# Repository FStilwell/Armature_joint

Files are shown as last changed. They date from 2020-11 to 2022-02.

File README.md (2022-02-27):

# Armature_joint
This repository serves as a location for relevant work regarding the Armature Joint module as my Level 7 Engineering Development Project at WelTec.

## Overview

In-depth details on the project can be found in the "project_report.pdf" file in the "documentation" folder.

### Mechanical Structure

The solidworks 3D files for the joint modules can be found in the "Mechanical_structure" folder. The solidworks files are quite messy with unorganised links in the model. Therefore, I would recommend that the concepts would be used rather than building directly from the solidworks files.

The details behind my thinking with the mechanical structure can be  found in the project report under the "5. Project Design/methodology" section.

### Electronics

All the electronics files and information are found under the "PCB" folder. More in-depth details on the electronics are found in the project report under the "5. Project Design/methodology" section.

#### Rework and test info

A document with the test info for each of the boards is found under the PCB/Board_testing directory. There are a few LEDs that were placed incorrectly and there's a design error with the reset button.

### Software

More details on the software can be found in the project report under the "5. Project Design/methodology" section.

The software that I worked on is found under SDKs/nRF5_SDK_14.2.0_17b948a/examples/my_examples. They are Segger Embedded Studio project files. There are two programs that I think might be useful which are the blinky projects below.

A blink program is found under SDKs/nRF5_SDK_14.2.0_17b948a/examples/my_examples/Armature_joint_blinky_4-working/

A BLE blink program is found under SDKs/nRF5_SDK_14.2.0_17b948a/examples/my_examples/ble_app_blinky-working/

#### Configuring projects to work with the Armature boards

A guide I wrote for configuring the Segger Embedded Studio example projects to work with the armature boards can be found at Documentation/Modifying_SDK_SES_examples_for_Armature.pdf

#### Programming the boards

Using the Segger J-Link Edu Mini and a custom ribbon cable with a 6 pin header, I was programming the boards using the native Segger Embedded Studio toolchain. The header is connected to to the board as shown in the image below.



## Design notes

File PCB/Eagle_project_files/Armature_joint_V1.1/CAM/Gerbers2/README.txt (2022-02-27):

Board Dimensions:
 Approximately 35mm X 35mm circular
 2 Layers
 1.6mm Thickness	
 Silkscreen on top layer only

Gerber Files:

copper_bottom.gbr - Bottom layer

copper_top.gbr - Top layer

Soldermask offset per your process.

Special Instructions:
No added copper around the PCB antenna where ground planes stop

Contact info:

traveler.hauptman@mechadept.com

022 627 1529

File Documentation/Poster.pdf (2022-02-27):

`

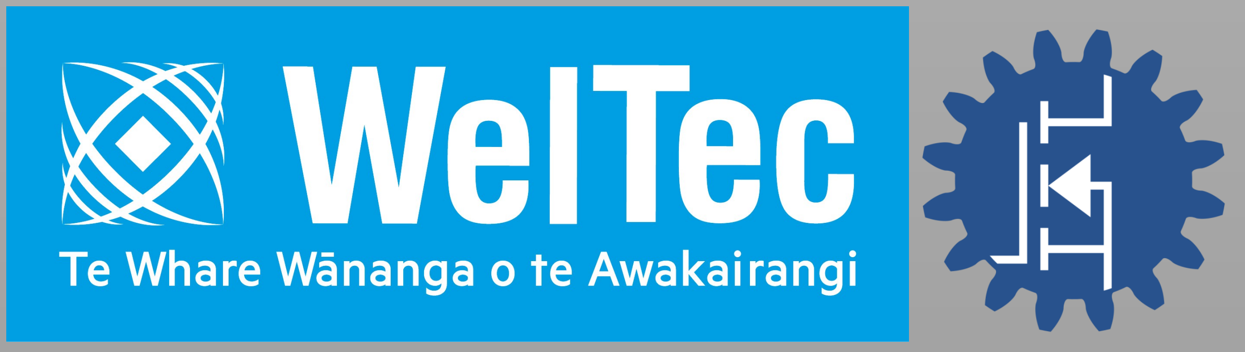
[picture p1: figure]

# Armature Joint Module

Prototyping large robots at a miniature scale is a great way to validate a robot’s design. It allows the engineer to test a robot’s kinematic structure design and its range of motion in the real world, at a low cost. MechAdept employs this method for their high-performance mechatronic systems, but they do not give useful joint position feedback without manual measurement. The aim of this project was to develop a functional prototype of a single joint module to prove the concept of a puppeteering armature which would be manipulated by hand and stream out position information to a user terminal via Bluetooth. This is for MechAdept to prototype robotics and present to clients a virtual puppeteered armature. The design had to be compact, battery powered, modular and simple.

By:
Flynn Stilwell

Supervisor:
Frank Beinersdorf

Client:
MechAdept

This project required the development of systems of three different types; mechanical, electronic, and embedded software.

LinkedIn

### Kinematic Structure

3D printing was used for its fast turnaround time of mechanical prototypes and its availability. 3D printing design considerations were then researched before designing concepts were produced.
The kinematic structure was rapidly prototyped using Solidworks 3D CAD software for the modelling and 3D printing for the manufacturing. Two main concepts were produced and evaluated, and the preferred one was iterated upon to experimentally validate design decisions. The first concept relied on the magnetic pull of a magnet to hold the links together and provide field position to the magnetic sensor, however the prevailing concept was a snap-fit type which relied on a clip-on profile to interface the two links. This offers a rigid connection, a holding torque due to friction in the joint interface and a simple solution.

Link 2: Holds the magnet with a press-fit and the male snap-fit tabs to interface with link 1.

Magnet: Diametrically magnetised for easy interface with the magnetic sensor on the PCB

Link 1: Provides the female slot for the snap-fit connection and an enclosure for the PCB and battery. The slot allows rotation of link 1 and provides friction and hence a holding torque.

Custom PCB: Powered by a Lithium-Polymer battery, the custom PCB features a Bluetooth-capable System on Chip (SoC), PCB trace antenna, 3D hall sensor for field position measurement, battery charging circuitry and a 3.3V voltage regulator.

Link 1 cap: Closes the enclosure and secures the PCB and battery.

# Overview

Prototype 4, disassembled

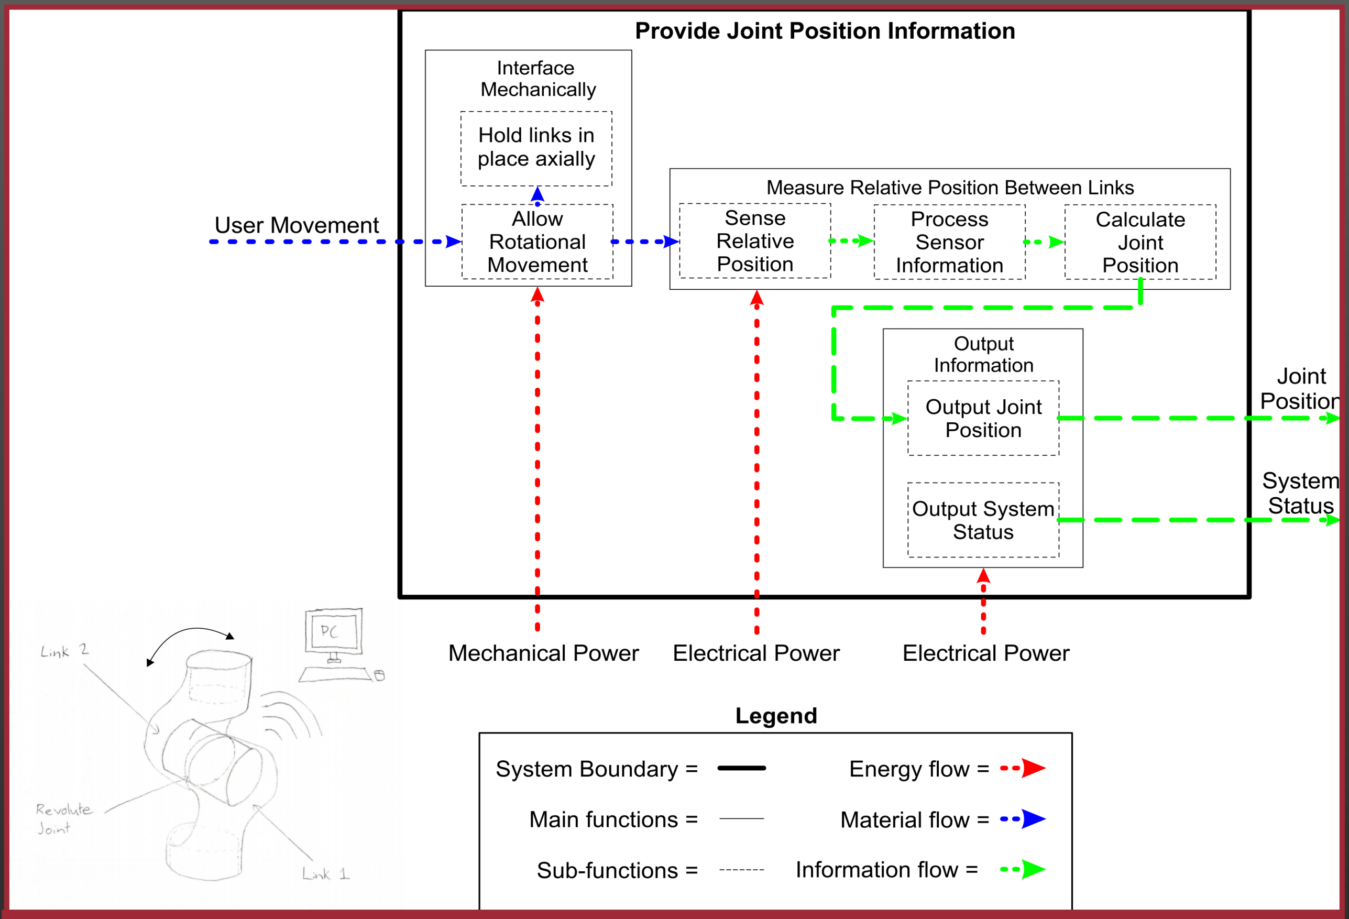
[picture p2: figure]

Function Structure Analysis for Problem identification

### Electronic System

The electronic system elements were prototyped on a breadboard to validate the magnetic position measurement system. High speed signal Printed Circuit Board (PCB) design considerations and electronic components were researched for implementing the design on a PCB. This was designed electronically using Autodesk Eagle, manufactured by PCBZone in NZ, and assembled with the help of MechAdept.
Reference circuitry from Nordic Semiconductor was used for the Bluetooth-capable System on Chip (SoC) section of the PCB to help ensure its sufficient Radio Frequency (RF) performance.

### Embedded Software

The Segger Embedded Studio Integrated Development Environment (IDE) was used to write software and program the custom board and nRF52 development dongle. Segger’s J-Link debugging probe was used with the IDE for code debugging. Nordic Semiconductor’s Software Development Kit (SDK) was used to learn the microcontroller platform and provide a base for the embedded software using the method of studying and modifying example code.

# Development

Assembly Process

Solder paste applied | Components Placed

Reflow soldering process

`

# Latest Prototype

Concept 1—magnetic
interface

Concept 2—Snap-fit interface

### Conclusion

Multiple mechanical test iterations have been produced and the best mechanical interface was found to be a snap-fit design with a balance of actuation friction, simplicity, and ease of assembly/disassembly.
Six of the PCB’s have been produced, all of which have passed power cycle tests, and one has been programmed with a basic Bluetooth application which verified the operation of the electronic system. The connection was maintained over a distance of >10m. The functionality of the joint remains unproven due to the complexity of the embedded software. The level of knowledge required was beyond the scope of this programme, but this project has presented the motivation for future learning.
This project involved the development of a single joint module. It provided the hardware platform to build upon. However, the vision is to have multiple of these connected to interchangeable links to provide a hand manipulated virtual model and miniature robot prototyping platform.

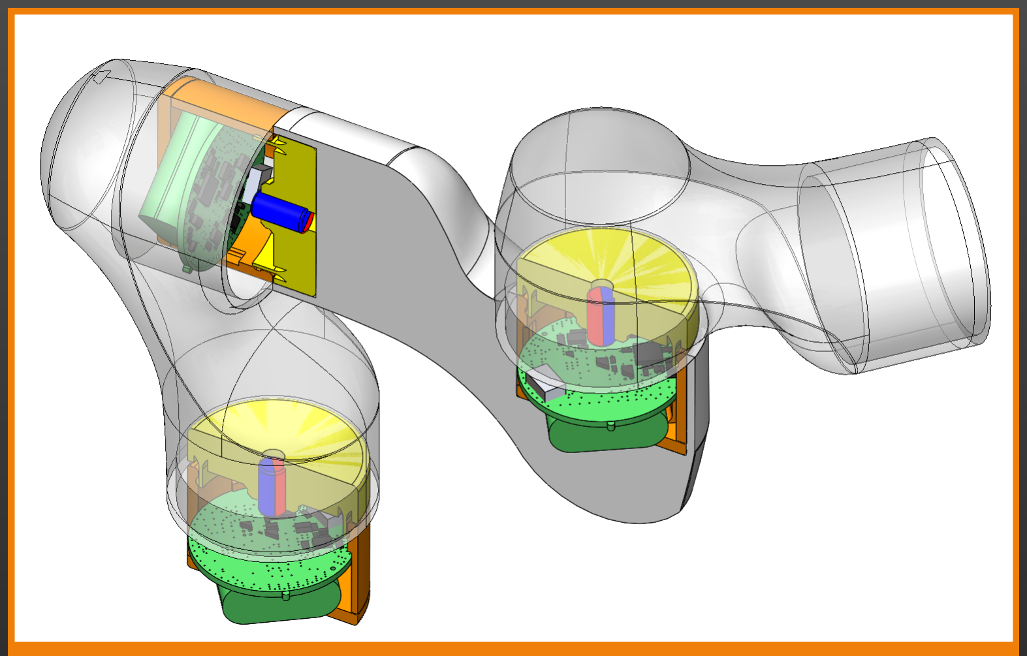
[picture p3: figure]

Envisioned armature implementation by Frank

Latest prototype
assembled,
indicating BLE
advertisement
with green LED

nRF42810 SoC

RGB indicator
LED

3.3V Voltage
Regulator

Lithium Polymer/
Ion battery charger

3D Hall Sensor

PCB trace antenna

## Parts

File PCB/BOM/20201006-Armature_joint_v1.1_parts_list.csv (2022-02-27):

Index | Quantity | Part Number | Manufacturer Part Number | Description | Customer Reference | Available | Backorder | Unit Price | Extended Price NZD
1 | 5 | 1490-1062-ND | NRF52810-QCAA-T | IC RF TXRX+MCU BLUETOOTH 32WFQFN |  | 5 | 0 | 5.30000 | 26.50
2 | 35 | 490-7998-1-ND | GCM155R71C104KA55J | CAP CER 0.1UF 16V X7R 0402 |  | 35 | 0 | 0.08900 | 3.12
3 | 10 | 311-1024-1-ND | CC0402JRNPO9BN101 | CAP CER 100PF 50V C0G/NPO 0402 |  | 10 | 0 | 0.03200 | 0.32
4 | 20 | 311-1446-1-ND | CC0603KRX7R7BB105 | CAP CER 1UF 16V X7R 0603 |  | 20 | 0 | 0.14000 | 2.80
5 | 25 | 311-3609-1-ND | CC0402GRNPO9BN120 | CAP CER 12PF 50V NPO 0402 |  | 25 | 0 | 0.08100 | 2.03
6 | 5 | 490-XRCGB32M000FXH2CR0CT-ND | XRCGB32M000FXH2CR0 | CRYSTAL 32.0000MHZ 8PF SMD |  | 5 | 0 | 0.74000 | 3.70
7 | 5 | CKN10503CT-ND | PTS810 SJK 250 SMTR LFS | SWITCH TACTILE SPST-NO 0.05A 16V |  | 5 | 0 | 0.54000 | 2.70
8 | 5 | 754-2143-1-ND | APHF1608LSEEQBDZGKC | LED RGB CLEAR 4SMD |  | 5 | 0 | 1.28000 | 6.40
9 | 20 | 311-330LRCT-ND | RC0402FR-07330RL | RES SMD 330 OHM 1% 1/16W 0402 |  | 20 | 0 | 0.02400 | 0.48
10 | 20 | 311-820LRCT-ND | RC0402FR-07820RL | RES SMD 820 OHM 1% 1/16W 0402 |  | 20 | 0 | 0.02400 | 0.48
11 | 6 | TC1015-3.3VCT713CT-ND | TC1015-3.3VCT713 | IC REG LINEAR 3.3V 100MA SOT23-5 |  | 6 | 0 | 0.61000 | 3.66
12 | 10 | 732-7499-1-ND | 885012205004 | CAP CER 470PF 10V X7R 0402 |  | 10 | 0 | 0.02400 | 0.24
13 | 5 | 609-5379-1-ND | 10118192-0002LF | CONN RCPT USB2.0 MICRO B SMD R/A |  | 5 | 0 | 0.71000 | 3.55
14 | 20 | 490-10884-1-ND | GRJ188C70J475KE11D | CAP CER 4.7UF 6.3V X7S 0603 |  | 20 | 0 | 0.35900 | 7.18
15 | 6 | MCP73831T-2ACI/OTCT-ND | MCP73831T-2ACI/OT | IC CONTROLLR LI-ION 4.2V SOT23-5 |  | 6 | 0 | 0.94000 | 5.64
16 | 6 | 475-3112-1-ND | LB QH9G-N1OO-35-1 | LED BLUE DIFFUSED 0402 SMD |  | 6 | 0 | 0.71000 | 4.26
17 | 20 | 311-10.0KLRCT-ND | RC0402FR-0710KL | RES SMD 10K OHM 1% 1/16W 0402 |  | 20 | 0 | 0.02400 | 0.48
18 | 20 | 311-1.20KLRCT-ND | RC0402FR-071K2L | RES SMD 1.2K OHM 1% 1/16W 0402 |  | 20 | 0 | 0.02400 | 0.48
19 | 10 | 490-11253-1-ND | GJM1555C1HR80WB01D | CAP CER 0.8PF 50V C0G/NP0 0402 |  | 10 | 0 | 0.27300 | 2.73
20 | 10 | 1276-1045-1-ND | CL10A475KQ8NNNC | CAP CER 4.7UF 6.3V X5R 0603 |  | 10 | 0 | 0.06900 | 0.69
21 | 5 | CW100505-3N9JCT-ND | CW100505-3N9J | FIXED IND 3.9NH 840MA 66MOHM SMD |  | 5 | 0 | 0.52000 | 2.60
22 | 5 | 644-1155-1-ND | NX3215SA-32.768K-STD-MUA-9 | CRYSTAL 32.7680KHZ 9PF SMD |  | 5 | 0 | 1.20000 | 6.00
23 | 10 | 587-3292-1-ND | BKP1005EM331-T | FERRITE BEAD 330 OHM 0402 1LN |  | 10 | 0 | 0.09300 | 0.93

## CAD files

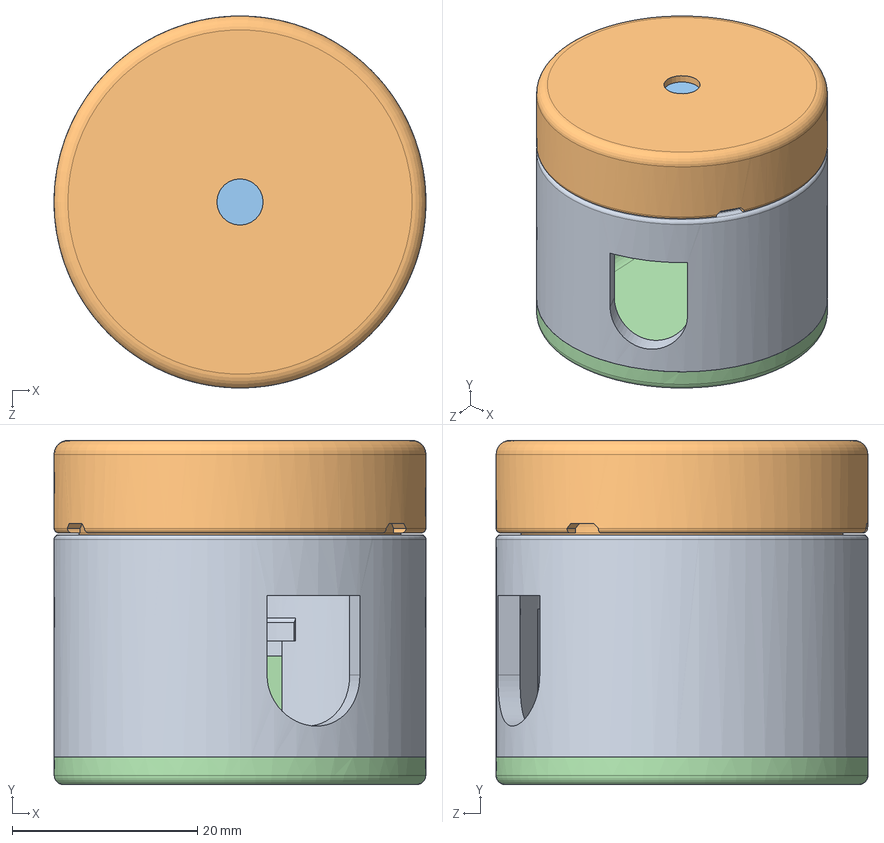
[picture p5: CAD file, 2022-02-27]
Mechanical_structure/Structure_v1.3.SLDASM
40.2 x 37.2 x 40.2 mm
Link1_v1.2
Link2_v1.3
Magnet_model
Link1_cap

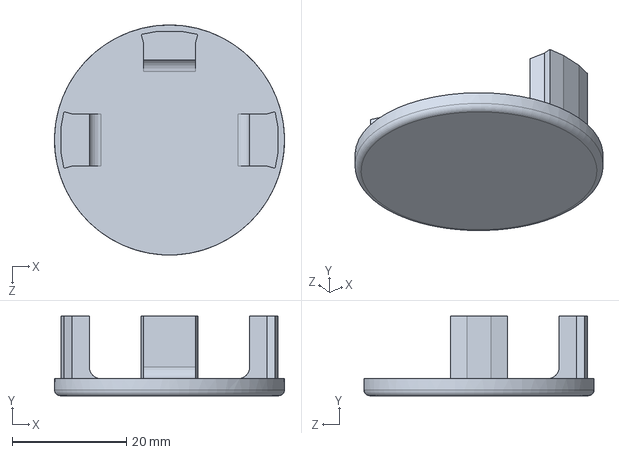
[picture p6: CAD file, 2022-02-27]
Mechanical_structure/Link1_cap.SLDPRT
40.2 x 13.9 x 40.2 mm

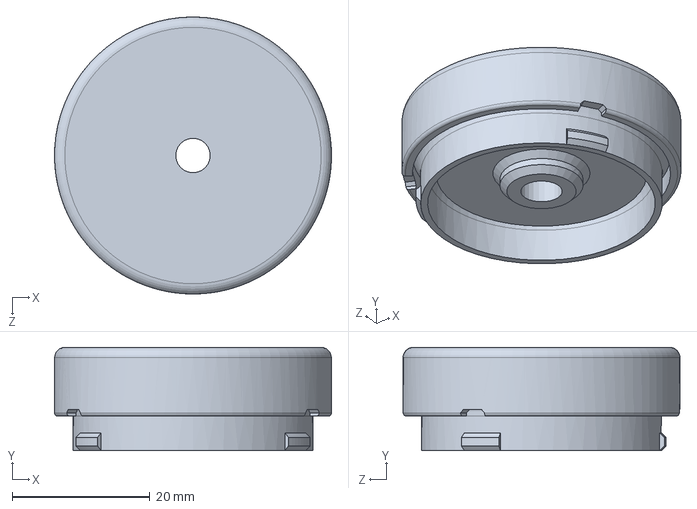
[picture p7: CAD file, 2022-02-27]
Mechanical_structure/Link2_v1.3.sldprt
40.2 x 15.0 x 40.2 mm

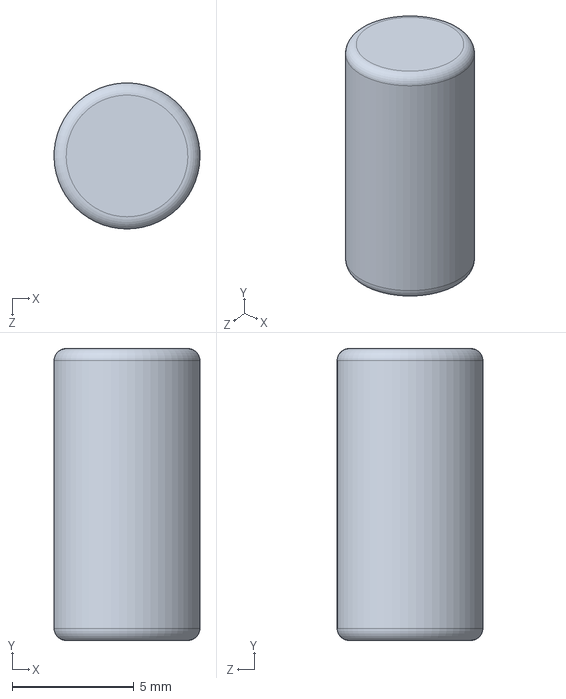
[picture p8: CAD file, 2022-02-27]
Mechanical_structure/Magnet_model.SLDPRT
6.00 x 12.0 x 6.00 mm

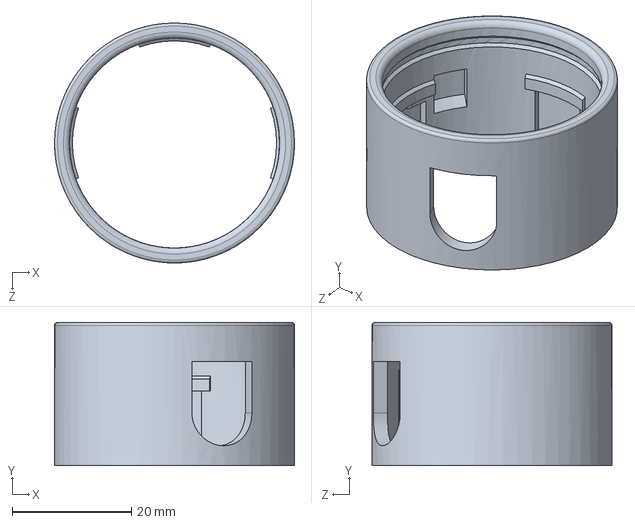
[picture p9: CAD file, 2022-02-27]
Mechanical_structure/Link1_v1.2.SLDPRT
40.2 x 24.0 x 40.2 mm

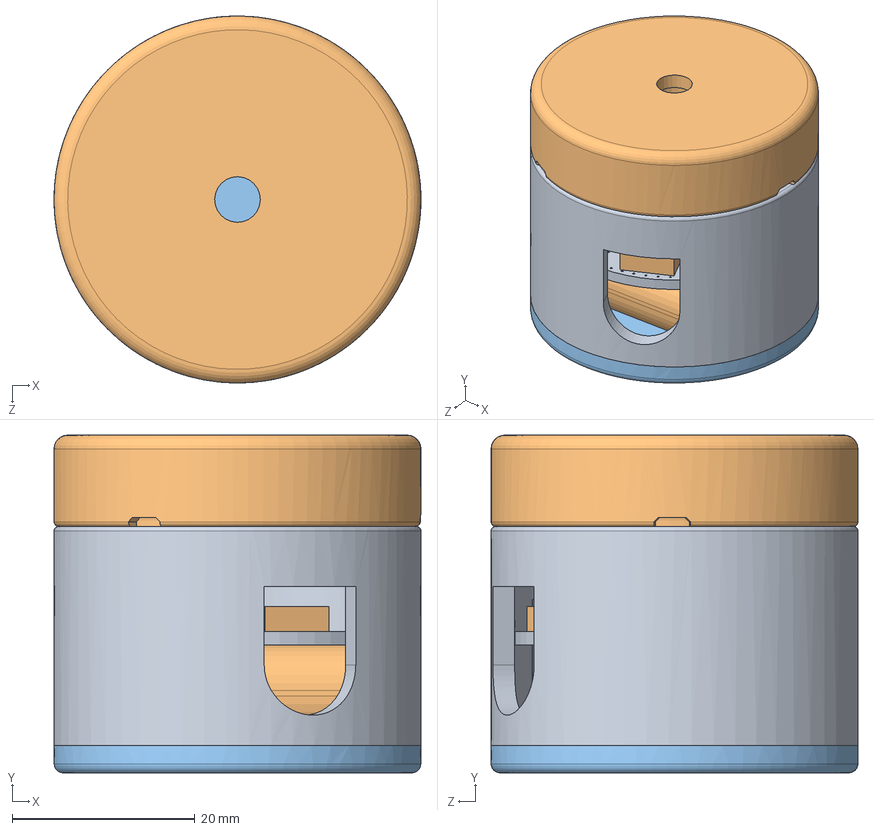
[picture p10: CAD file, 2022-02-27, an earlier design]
Mechanical_structure/Structure_v1.1.SLDASM
40.2 x 37.0 x 40.2 mm
Link1_v1.1
Link2_v1.3
Magnet_model
APHF1608SEEQBDZGKC_KNB-L.step
BT-XTAL_2016_N.step
LED_SML-LX0402SYC-TR_LUM-M.step
PG-TSOP6-6-5_INF.step
PTS810.step
QFN50P500X500X90-32_N.step
RESC0402_M.step x 4
RESC0402_N.step x 20
RESC0603_N.step x 8
SOT-23-5_MC_MCH.step
SOT23-5.step
SWD_6P.step
XTAL_3215_N.step
Board.step
Part1^Armature_Joint_PCB_V1.1
Link1_cap

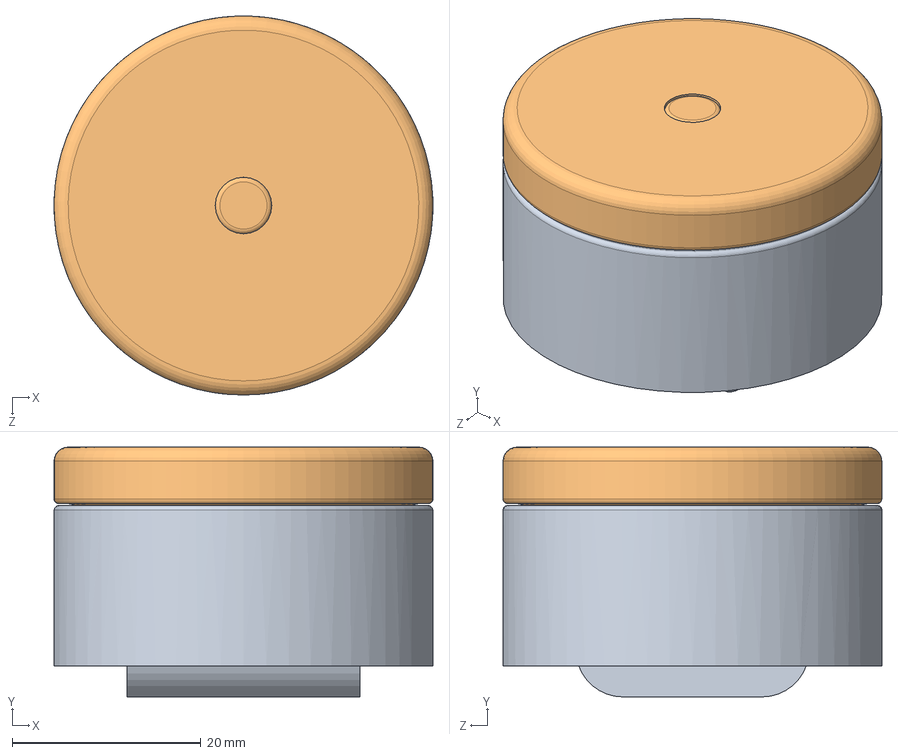
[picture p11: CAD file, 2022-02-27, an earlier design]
Mechanical_structure/Structure_v1.0.SLDASM
40.2 x 26.5 x 40.2 mm
Link1_v1
Link2_v1
APHF1608SEEQBDZGKC_KNB-L.step
BT-XTAL_2016_N.step
LED_SML-LX0402SYC-TR_LUM-M.step
PG-TSOP6-6-5_INF.step
PTS810.step
QFN50P500X500X90-32_N.step
RESC0402_M.step x 4
RESC0402_N.step x 20
RESC0603_N.step x 8
SOT-23-5_MC_MCH.step
SOT23-5.step
SWD_6P.step
XTAL_3215_N.step
Board.step
Part1^Armature_Joint_PCB_V1.1
Magnet_model

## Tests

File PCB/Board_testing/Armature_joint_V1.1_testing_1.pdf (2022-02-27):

PCB Name | Armature Joint V1.1
Serial Number | 3
Tester | Flynn Stilwell
Test Point Diagram

Top View
Test Points | Test Parameters / Conditions | Criterion, Units | Value | Comments
Multimeter Probes | No power connected | Resistance, Ω | 0.1
1-2 | | | OL
1-3 | | | 9.78k
1-4 | | | OL
1-10 | | | 0.0
1-6 | | | 0.0 | Check button, all pins connected to GND. Button pin 4 connected to GND
1-7 | | | 6.12M
1-8 | | | OL
1-9 | | | 6.15M
1-2
1-3 | USB Power Only | Voltage, V
1-4
1-2
1-3 | Battery Power Only | Voltage, V
1-4

Notes:

11.11.20
- RGB LED orientation is wrong
- Button is not functioning due to schematic error, should be removed

PCB Name | Armature Joint V1.1
Serial Number | 4
Tester | Flynn Stilwell
Test Point Diagram

Top View
Test Points | Test Parameters / Conditions | Criterion, Units | Value | Comments
Multimeter Probes | No power connected | Resistance, Ω | 0.3
1-2 | | | OL
1-3 | | | 9.82k | Value from pullup resistor R8, related to GND’d switch
1-4 | | | OL
1-10 | | | 0.1
1-6 | | | 0.1 | Check button, all pins connected to GND. Button pin 4 connected to GND
1-7 | | | 47.2k
1-8 | | | OL
1-9 | | | 6.52M
1-2 | USB Power Only | Voltage, V | 3.987
1-3 | | | 3.343
1-4 | | | 5.074
USB Tester | | Current, A
1-2 | Battery Power Only | Voltage, V 1-3
USB Tester | Power, W

Battery + USB, Charging battery | Current, A
| Voltage, V

Notes:
11.11.20
- RGB LED orientation is wrong
- Button is not functioning due to schematic error, should be removed

PCB Name | Armature Joint V1.1
Serial Number | 5
Tester | Flynn Stilwell
Test Point Diagram

Top View
Test Points | Test Parameters / Conditions | Criterion, Units | Value | Comments
Multimeter Probes | No power connected | Resistance, Ω
1-2 | | | OL
1-3 | | | 9.84k | Value from pullup resistor R8, related to GND’d switch
1-4 | | | OL
1-10 | | | 0.2
1-6 | | | 0.2 | Check button, all pins connected to GND. Button pin 4 connected to GND
1-7 | | | 47.48k
1-8 | | | 9.84k
1-9 | | | 152.0k
1-2
1-3 | USB Power Only | Voltage, V
1-4
1-2
1-3 | Battery Power Only | Voltage, V
1-4

Notes:
11.11.20
- LD2, charger indicator orientation is wrong
- BLE Blinky program upload: Indicates advertisement but cannot be found with nRF Connect Android
- C1 possibly disconnected
- Button is not functioning due to schematic error, should be removed

PCB Name | Armature Joint V1.1
Serial Number | 6
Tester | Flynn Stilwell
Test Point Diagram

Top View
Test Points | Test Parameters / Conditions | Criterion, Units | Value | Comments
Multimeter Probes | No power connected | Resistance, Ω | 0.2
1-2 | | | OL
1-3 | | | 9.80k | Value from pullup resistor R8, related to GND’d switch
1-4 | | | OL
1-10 | | | 0.1
1-6 | | | 0.2 | Check button, all pins connected to GND. Button pin 4 connected to GND
1-7 | | | 47.92k
1-8 | | | 9.80k
1-9 | | | 156.0k | Lower than S/N 3 and 4
1-2 | USB Power Only | Voltage, V | 4.060
1-3 | | | 3.328
1-4 | | | 5.072
USB Tester | | Current, A | 0.000 | No current draw, no shorts
1-2
1-3 | Battery Power Only | Voltage, V
1-4

Notes:
- Removed Button
- R4 and R5 needed more solder on their uC pin pads

PCB Name | Armature Joint V1.1
Serial Number | 1
Tester | Flynn Stilwell
Test Point Diagram

Top View
Test Points | Test Parameters / Conditions | Criterion, Units | Value | Comments
Multimeter Probes | No power connected | Resistance, Ω
1-2 | | | OL
1-3 | | | 9.82k | Value from pullup resistor R8, related to GND’d switch
1-4 | | | OL
1-10 | | | 0.2
1-6 | | | 0.2 | Check button, all pins connected to GND. Button pin 4 connected to GND
1-7 | | | 45.53k
1-8 | | | 9.82k
1-9 | | | 148.7k
1-2 | USB Power Only | Voltage, V | 4.062
1-3 | | | 3.327
1-4 | | | 5.048
1-2 | Battery Power Only | Voltage, V | 3.860
1-3 | | | 3.328
1-4 | | | 0.515

Notes:
11.11.20
- RGB LED orientation is wrong
- Button is not functioning due to schematic error, should be removed

PCB Name | Armature Joint V1.1
Serial Number | 2
Tester | Flynn Stilwell
Test Point Diagram

Top View
Test Points | Test Parameters / Conditions | Criterion, Units | Value | Comments
Multimeter Probes | No power connected | Resistance, Ω
1-2 | | | OL
1-3 | | | 9.80k | Value from pullup resistor R8, related to GND’d switch
1-4 | | | OL
1-10 | | | 0.2
1-6 | | | 0.2 | Check button, all pins connected to GND. Button pin 4 connected to GND
1-7 | | | 47.64k
1-8 | | | 9.80k
1-9 | | | 0.955M | Lower than S/N 3 and 4, higher than 6
1-2 | USB Power Only | Voltage, V | -0.155 | Issue with charger IC. Pin 1, Stat = ~0V Pin 2, GND = 0.0V Pin 3, VBAT = -120mV Pin 4, VDD = 5.109V Pin 5, Prog = ~0V

1-3 | 0.0
1-4 | 5.109
1-2
1-3 | Battery Power Only | Voltage, V
1-4

Notes:
11.11.20
- LD2, charger indicator orientation is wrong
- Charger IC is not working
- Button is not functioning due to schematic error, should be removed

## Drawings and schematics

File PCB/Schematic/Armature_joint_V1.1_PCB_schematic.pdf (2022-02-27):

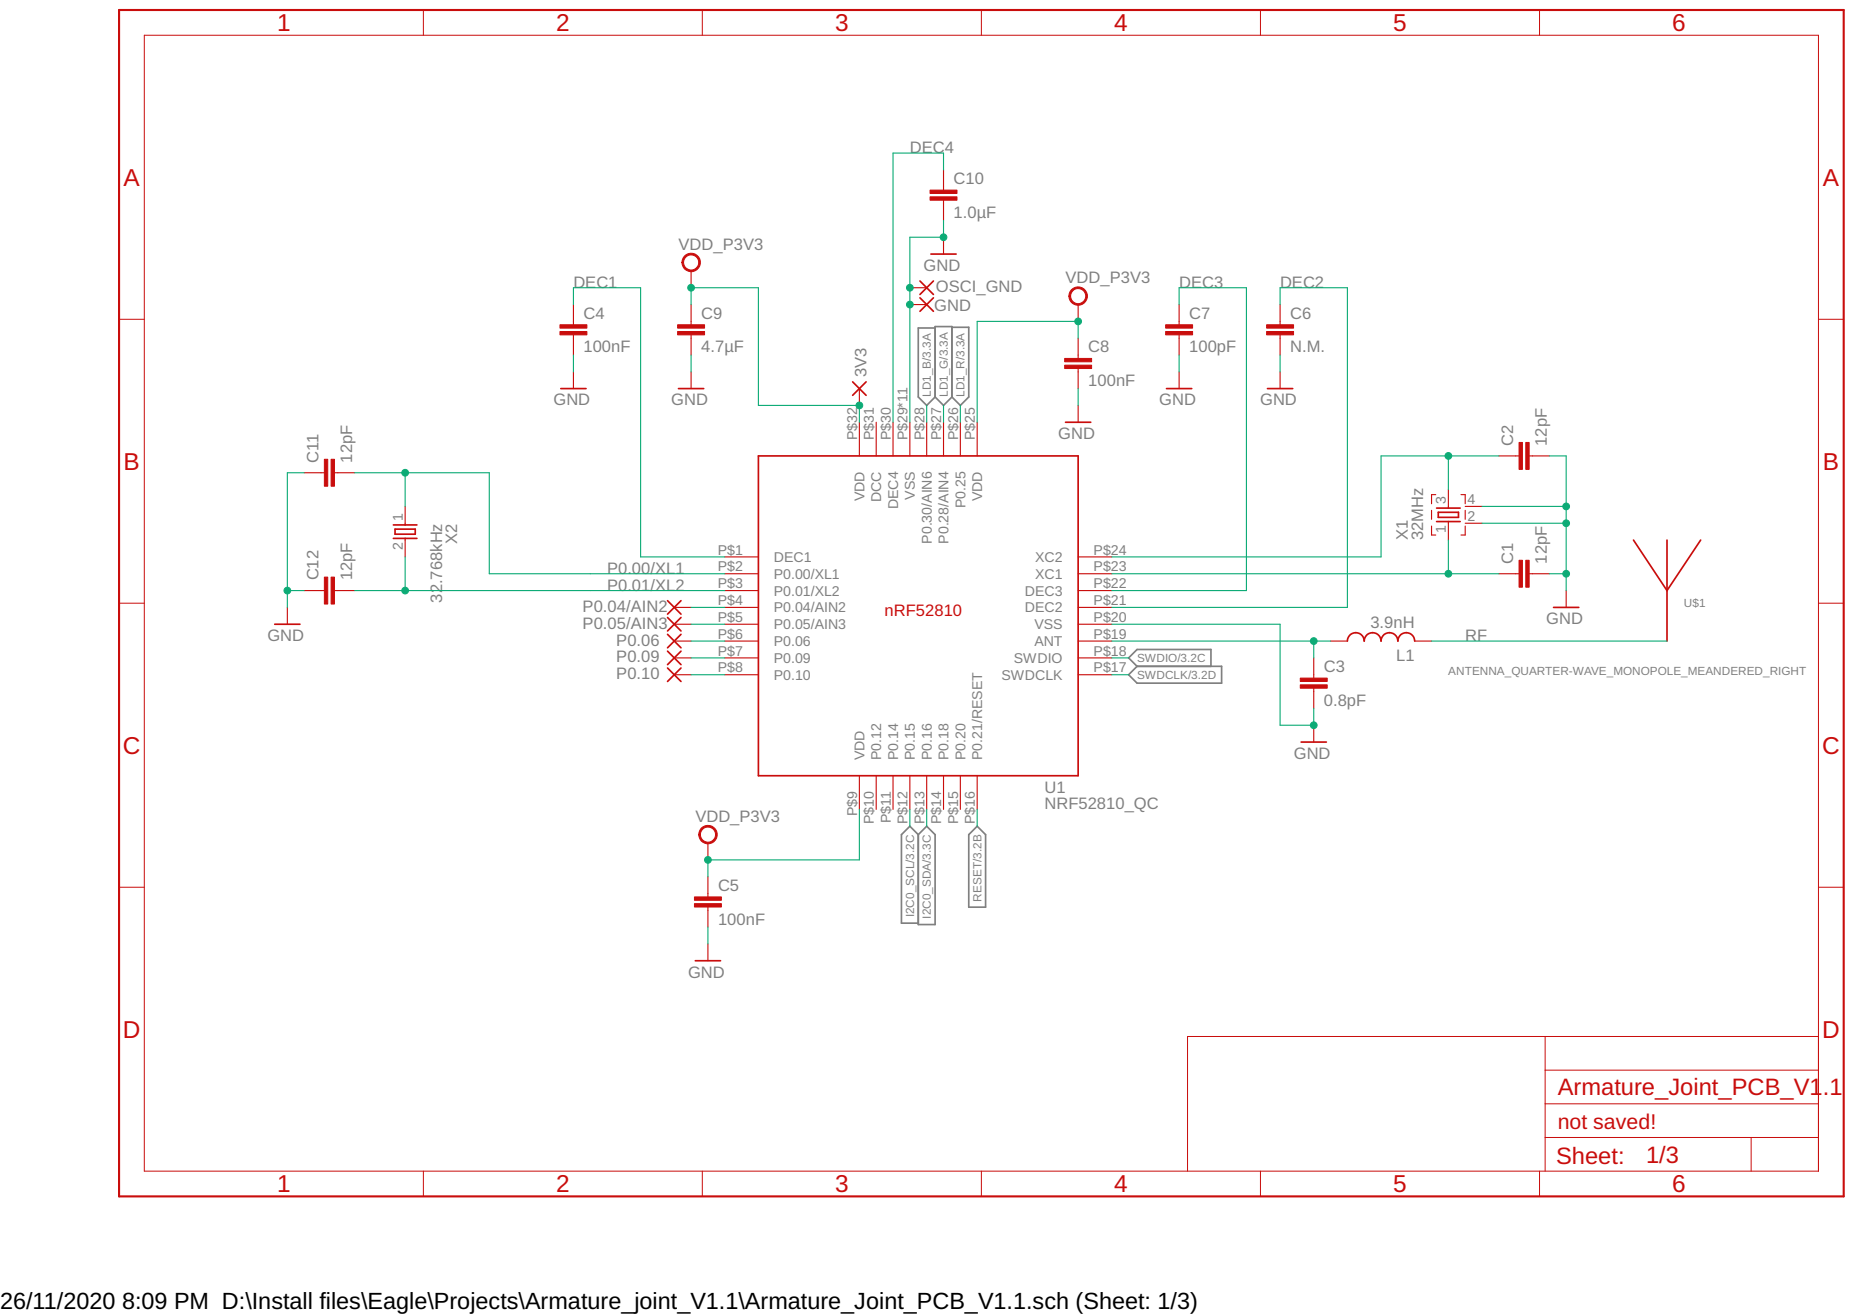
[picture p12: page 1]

26/11/2020 8:09 PM D:\Install files\Eagle\Projects\Armature_joint_V1.1\Armature_Joint_PCB_V1.1.sch (Sheet: 1/3)

LD2

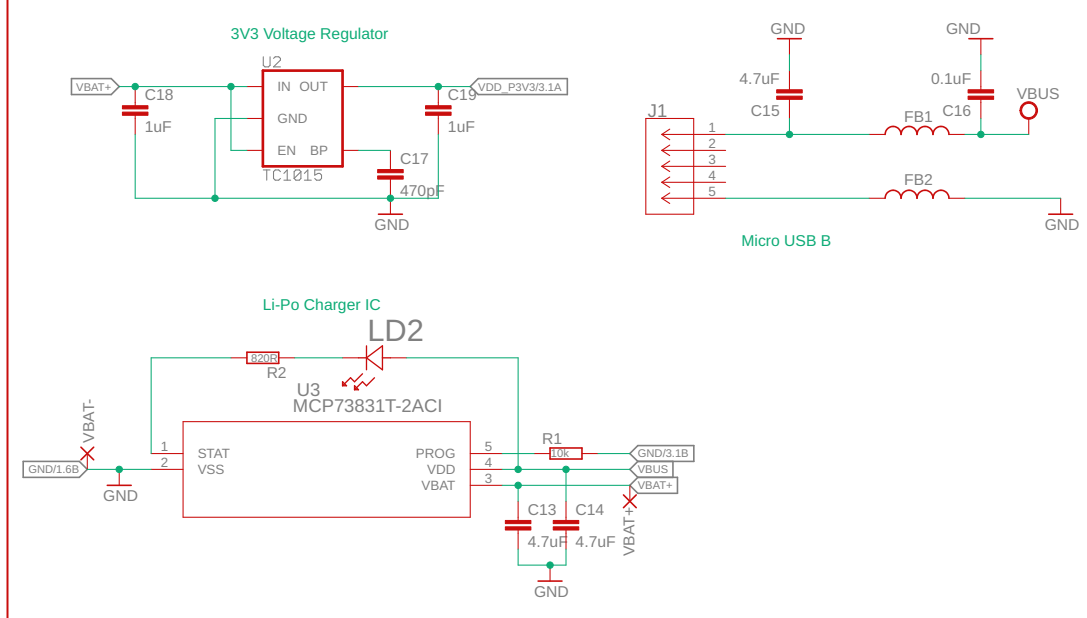
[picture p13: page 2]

Li-Po Charger IC

Document Number: | REV:

Date: 26/11/2020 8:11 PM | Sheet: 2/3

26/11/2020 8:11 PM D:\Install files\Eagle\Projects\Armature_joint_V1.1\Armature_Joint_PCB_V1.1.sch (Sheet: 2/3)

LD1

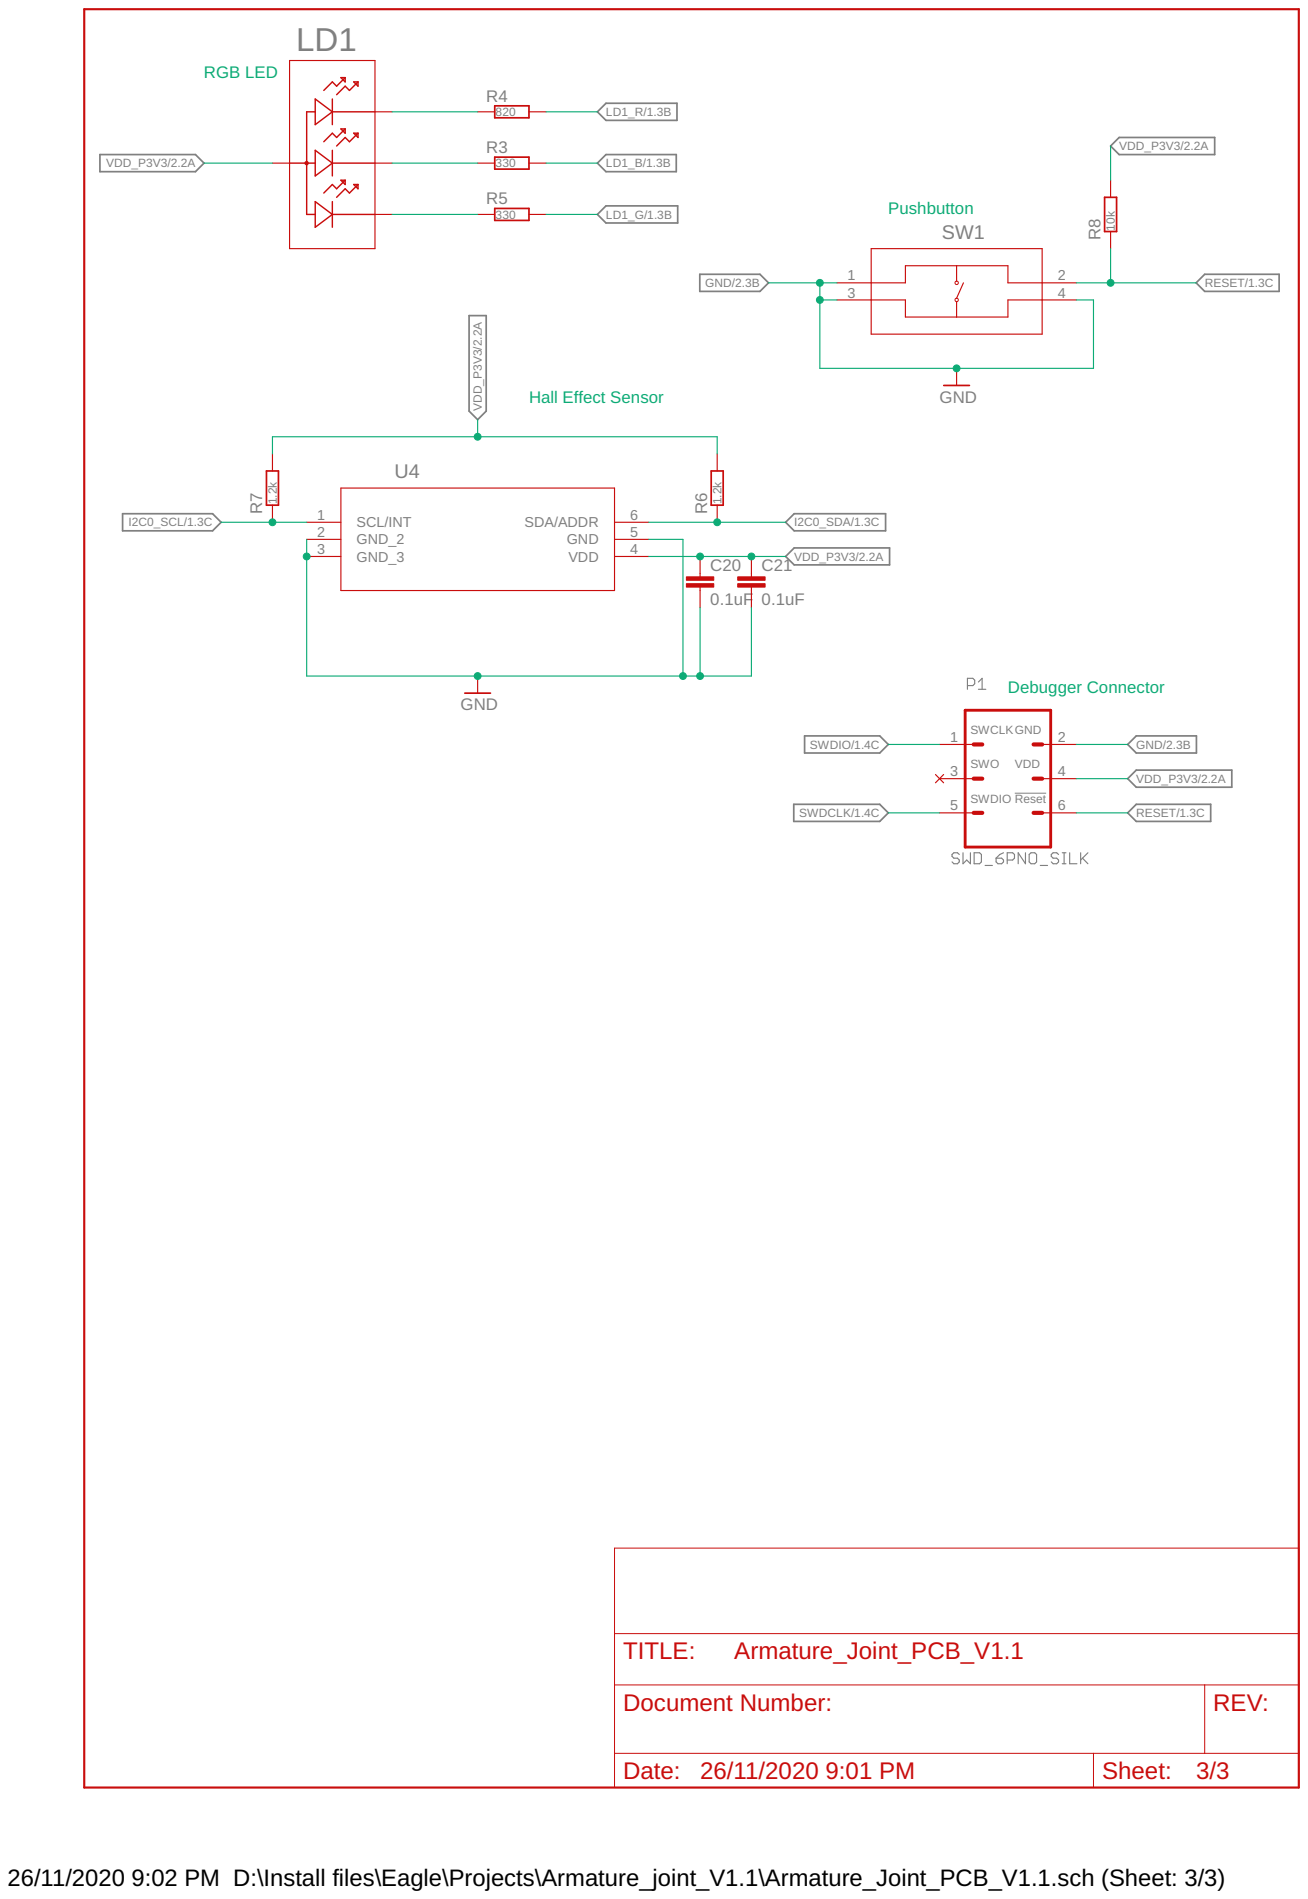
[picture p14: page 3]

Document Number: | REV:

Date: 26/11/2020 9:01 PM | Sheet: 3/3

26/11/2020 9:02 PM D:\Install files\Eagle\Projects\Armature_joint_V1.1\Armature_Joint_PCB_V1.1.sch (Sheet: 3/3)

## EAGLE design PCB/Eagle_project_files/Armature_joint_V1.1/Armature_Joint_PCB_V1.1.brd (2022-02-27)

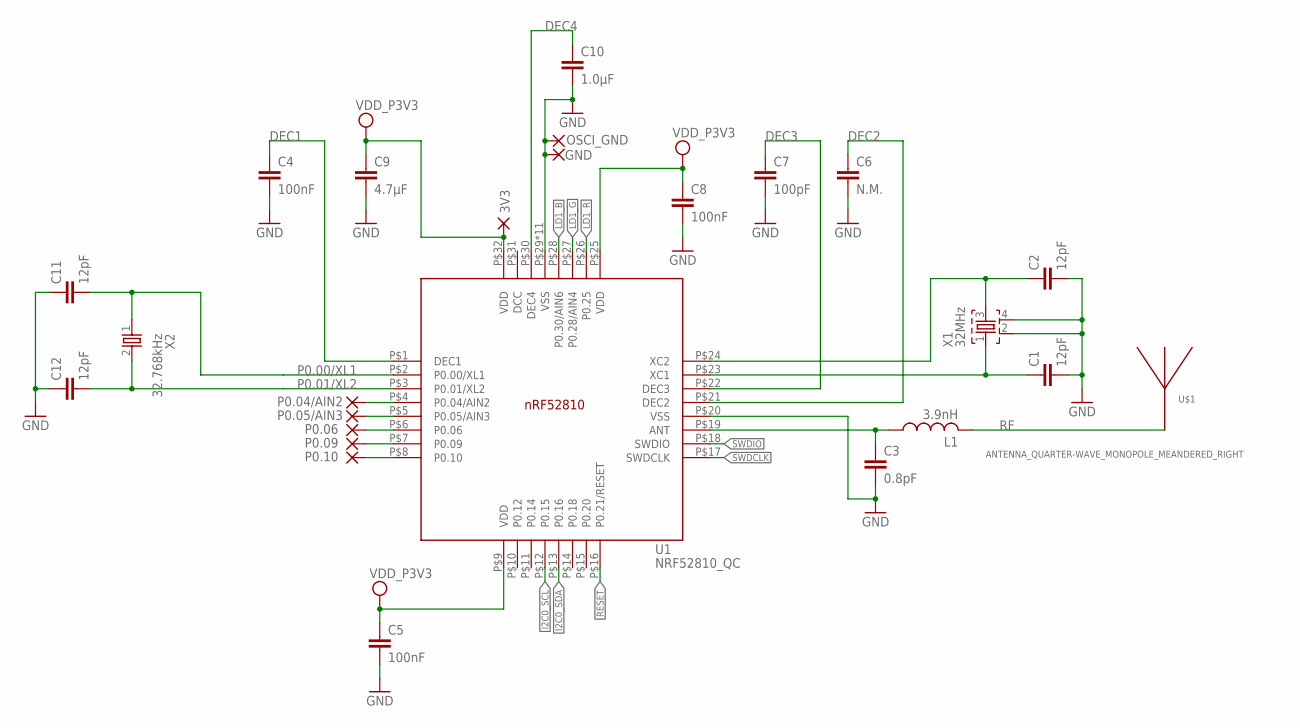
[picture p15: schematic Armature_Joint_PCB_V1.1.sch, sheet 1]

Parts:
3V3: vdd_p3v3; SMD1,27-2,54
C1, C2, C11, C12: 12pF; RESC0402_N
C3: 0.8pF; RESC0402_N
C4, C5, C8: 100nF; RESC0402_N
C6: N.M.; RESC0402_N
C7: 100pF; RESC0402_N
C9: 4.7µF; RESC0603_N
C10: 1.0µF; RESC0603_N
GND: GND; SMD1,27-2,54
L1: 3.9nH; RESC0402_N
OSCI_GND: GND; 2,15/1,0
P0.04/AIN2: P0.04/AIN2; SMD1,27-2,54
P0.05/AIN3: P0.05/AIN3; SMD1,27-2,54
P0.06: P0.06; SMD1,27-2,54
P0.09: P0.09; SMD1,27-2,54
P0.10: P0.10; SMD1,27-2,54
U1: NRF52810_QC; QFN50P500X500X90-32_N
U$1: ANTENNA_QUARTER-WAVE_MONOPOLE_MEANDERED_RIGHT; QWMP_MEANDERED_RIGHT_+6
X1: 32MHz; BT-XTAL_2016_N
X2: 32.768kHz; XTAL_3215_N

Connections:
ANT: C3.1, L1.1, U1.P$19 (ANT)
DEC1: C4.1, U1.P$1 (DEC1)
DEC2: C6.1, U1.P$21 (DEC2)
DEC3: C7.1, U1.P$22 (DEC3)
DEC4: C10.1, U1.P$30 (DEC4)
GND: C1.2, C2.2, C3.2, C4.2, C5.2, C6.2, C7.2, C8.2, C9.2, C10.2, C11.1, C12.1, GND.1, OSCI_GND.1, U1.P$20 (VSS), U1.P$29 (VSS), U1.P$33 (VSS), U1.P$34 (VSS), U1.P$35 (VSS), U1.P$36 (VSS), U1.P$37 (VSS), U1.P$38 (VSS), U1.P$39 (VSS), U1.P$40 (VSS), U1.P$41 (VSS), U1.P$42 (VSS), X1.2, X1.4; also elsewhere on the board
I2C0_SCL: U1.P$12 (P0.15); also elsewhere on the board
I2C0_SDA: U1.P$13 (P0.16); also elsewhere on the board
LD1_B: U1.P$28 (P0.30/AIN6); also elsewhere on the board
LD1_G: U1.P$27 (P0.28/AIN4); also elsewhere on the board
LD1_R: U1.P$26 (P0.25); also elsewhere on the board
unnamed: C2.1, U1.P$24 (XC2), X1.3
P0.00/XL1: C11.2, U1.P$2 (P0.00/XL1), X2.1
P0.01/XL2: C12.2, U1.P$3 (P0.01/XL2), X2.2
P0.04/AIN2: P0.04/AIN2.1, U1.P$4 (P0.04/AIN2)
P0.05/AIN3: P0.05/AIN3.1, U1.P$5 (P0.05/AIN3)
P0.06: P0.06.1, U1.P$6 (P0.06)
P0.09: P0.09.1, U1.P$7 (P0.09)
P0.10: P0.10.1, U1.P$8 (P0.10)
RESET: U1.P$16 (P0.21/RESET); also elsewhere on the board
RF: L1.2, U$1.P$1
SWDCLK: U1.P$17 (SWDCLK); also elsewhere on the board
SWDIO: U1.P$18 (SWDIO); also elsewhere on the board
VDD_P3V3: 3V3.1, C5.1, C8.1, C9.1, U1.P$9 (VDD), U1.P$25 (VDD), U1.P$32 (VDD); also elsewhere on the board
X1: C1.1, U1.P$23 (XC1), X1.1

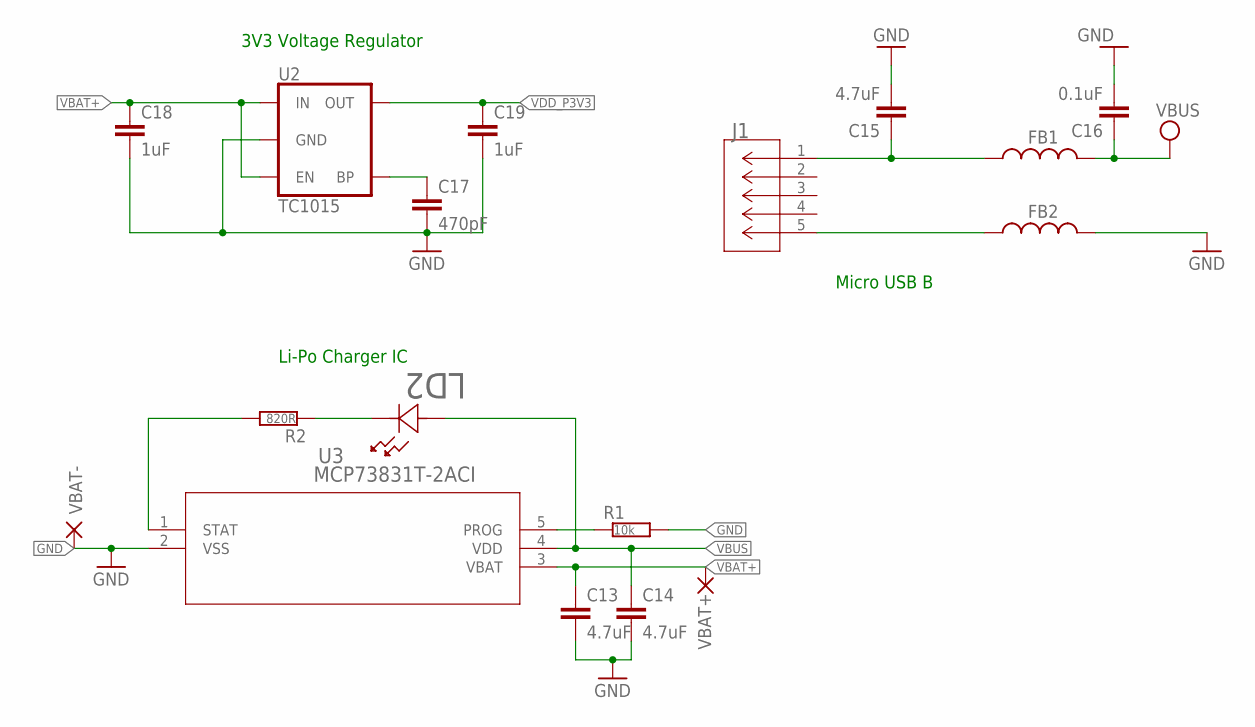
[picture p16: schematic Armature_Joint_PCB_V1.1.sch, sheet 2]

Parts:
C13, C14, C15: 4.7uF; RESC0603_N
C16: 0.1uF; RESC0603_N
C17: 470pF; RESC0402_N
C18, C19: 1uF; RESC0603_N
FB1, FB2: FERRITE_BEAD; RESC0402_M
J1: 10118192-0002LF; CONN_10118192-0002LF_AMP
LD2: LBQH9G-N1OO-35-1; LED_SML-LX0402SYC-TR_LUM-M
R1: 10k; RESC0402_N
R2: 820R; RESC0402_N
U2: TC1015; SOT23-5
U3: MCP73831T-2ACI; SOT-23-5_MC_MCH
VBAT+: VBAT+; SMD1,27-2,54
VBAT-: GND; SMD1,27-2,54

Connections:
GND: C13.2, C14.2, C15.2, C16.2, C17.2, C18.2, C19.2, FB2.2, R1.2, U2.2 (GND), U3.2 (VSS), VBAT-.1; also elsewhere on the board
unnamed: LD2.1, R2.1
unnamed: C17.1, U2.4 (BP)
unnamed: R1.1, U3.5 (PROG)
unnamed: R2.2, U3.1 (STAT)
unnamed: C15.1, FB1.1, J1.1
unnamed: FB2.1, J1.5
VBAT+: C13.1, C18.1, U2.1 (IN), U2.3 (EN), U3.3 (VBAT), VBAT+.1
VBUS: C14.1, C16.1, FB1.2, LD2.2, U3.4 (VDD)
VDD_P3V3: C19.1, U2.5 (OUT); also elsewhere on the board

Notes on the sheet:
3V3 Voltage Regulator
Li-Po Charger IC
Micro USB B

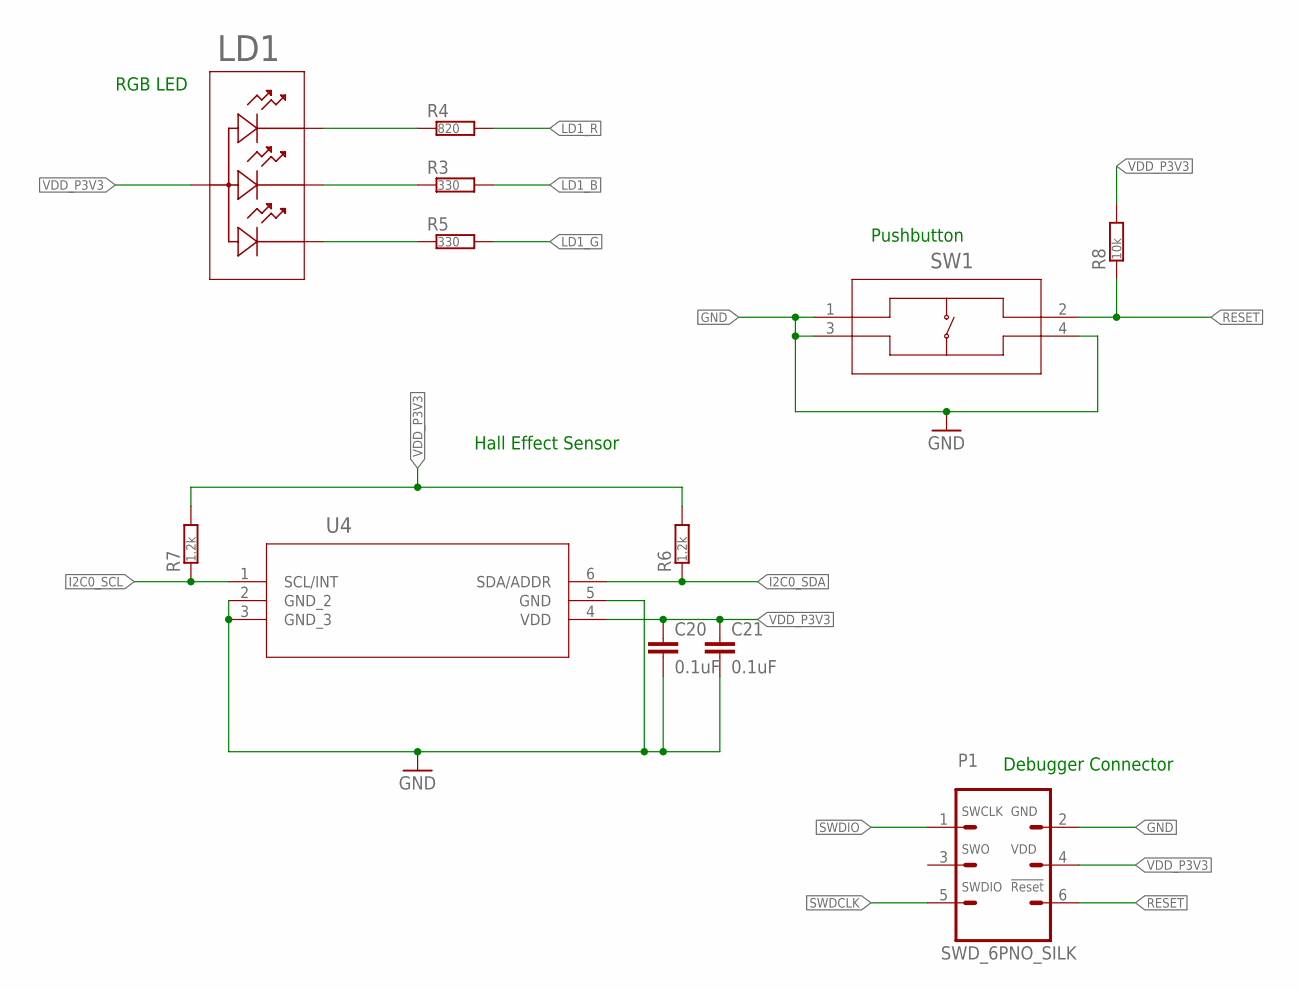
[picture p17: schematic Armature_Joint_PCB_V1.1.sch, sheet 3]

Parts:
C20, C21: 0.1uF; RESC0402_M
LD1: APHF1608SEEQBDZGKCAPHF1608SEEQBDZGKC_KNB-L; APHF1608SEEQBDZGKC_KNB-L
P1: SWD_6PNO_SILK; SWD_6P
R3, R5: 330; RESC0402_N
R4: 820; RESC0402_N
R6, R7: 1.2k; RESC0402_N
R8: 10k; RESC0402_N
SW1: PTS810SJG250SMTRLFS; PTS810
U4: TLV493DA1B6HTSA2; PG-TSOP6-6-5_INF

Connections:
GND: C20.2, C21.2, P1.2, SW1.1, SW1.3, SW1.4, U4.2 (GND_2), U4.3 (GND_3), U4.5 (GND); also elsewhere on the board
I2C0_SCL: R7.1, U4.1 (SCL/INT); also elsewhere on the board
I2C0_SDA: R6.1, U4.6 (SDA/ADDR); also elsewhere on the board
LD1_B: R3.2; also elsewhere on the board
LD1_G: R5.2; also elsewhere on the board
LD1_R: R4.2; also elsewhere on the board
unnamed: LD1.4, R5.1
unnamed: LD1.3, R3.1
unnamed: LD1.2, R4.1
RESET: P1.6, R8.1, SW1.2; also elsewhere on the board
SWDCLK: P1.5; also elsewhere on the board
SWDIO: P1.1; also elsewhere on the board
VDD_P3V3: C20.1, C21.1, LD1.1, P1.4, R6.2, R7.2, R8.2, U4.4 (VDD); also elsewhere on the board

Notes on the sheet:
Pushbutton
RGB LED
Hall Effect Sensor
Debugger Connector

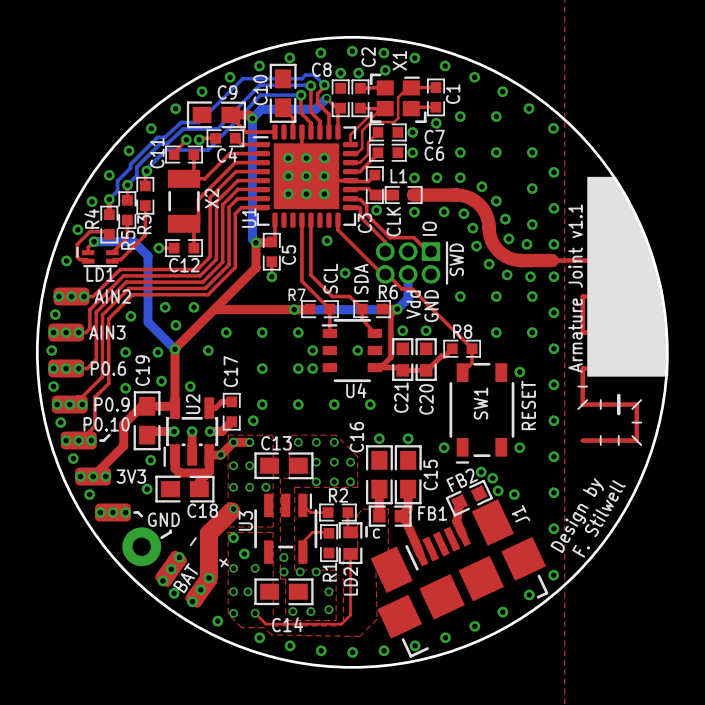
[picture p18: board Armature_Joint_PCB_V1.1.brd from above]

Board: 2 copper layers, 35.0 x 35.0 mm, 54 parts (0 on the bottom side), 36 nets.

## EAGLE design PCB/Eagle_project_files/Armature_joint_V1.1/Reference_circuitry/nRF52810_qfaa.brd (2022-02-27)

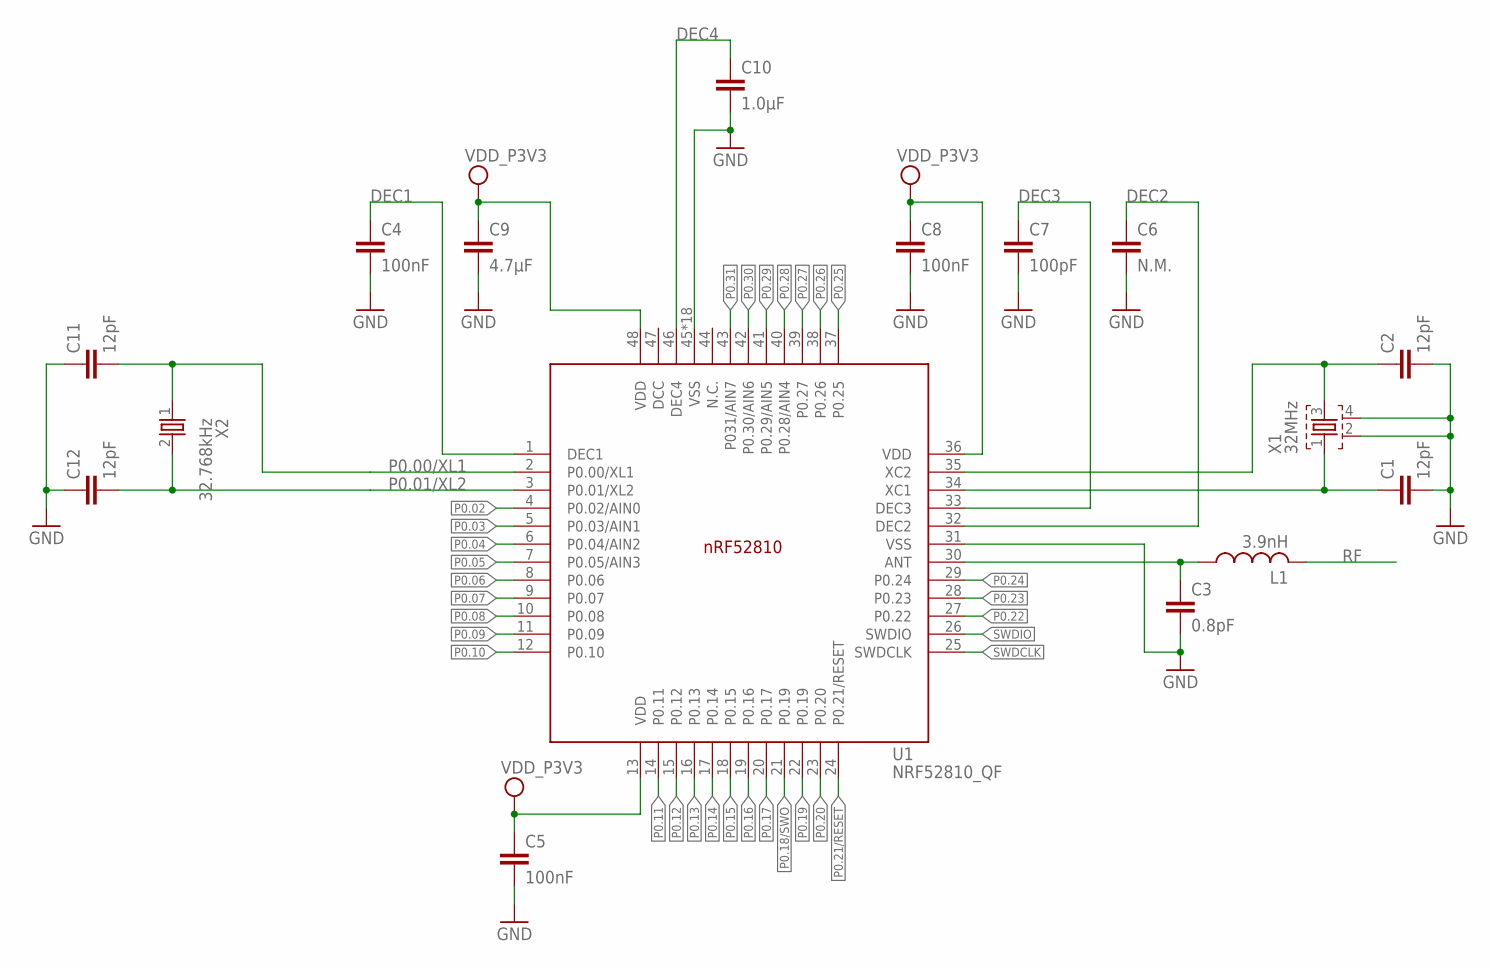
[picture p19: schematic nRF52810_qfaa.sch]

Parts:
C1, C2, C11, C12: 12pF; RESC0402_N
C3: 0.8pF; RESC0402_N
C4, C5, C8: 100nF; RESC0402_N
C6: N.M.; RESC0402_N
C7: 100pF; RESC0402_N
C9: 4.7µF; RESC0603_N
C10: 1.0µF; RESC0603_N
L1: 3.9nH; RESC0402_N
U1: NRF52810_QF; QFN40P600X600X90-48_N
X1: 32MHz; BT-XTAL_2016_N
X2: 32.768kHz; XTAL_3215_N

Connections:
ANT: C3.1, L1.1, U1.30 (ANT)
DEC1: C4.1, U1.1 (DEC1)
DEC2: C6.1, U1.32 (DEC2)
DEC3: C7.1, U1.33 (DEC3)
DEC4: C10.1, U1.46 (DEC4)
GND: C1.2, C2.2, C3.2, C4.2, C5.2, C6.2, C7.2, C8.2, C9.2, C10.2, C11.1, C12.1, U1.31 (VSS), U1.45 (VSS), U1.PAD (VSS), U1.PAD@VIA01 (VSS), U1.PAD@VIA02 (VSS), U1.PAD@VIA03 (VSS), U1.PAD@VIA04 (VSS), U1.PAD@VIA05 (VSS), U1.PAD@VIA06 (VSS), U1.PAD@VIA07 (VSS), U1.PAD@VIA08 (VSS), U1.PAD@VIA09 (VSS), U1.PAD@VIA10 (VSS), U1.PAD@VIA11 (VSS), U1.PAD@VIA12 (VSS), U1.PAD@VIA13 (VSS), U1.PAD@VIA14 (VSS), U1.PAD@VIA15 (VSS), U1.PAD@VIA16 (VSS), X1.2, X1.4
unnamed: C2.1, U1.35 (XC2), X1.3
P0.00/XL1: C11.2, U1.2 (P0.00/XL1), X2.1
P0.01/XL2: C12.2, U1.3 (P0.01/XL2), X2.2
P0.02: U1.4 (P0.02/AIN0)
P0.03: U1.5 (P0.03/AIN1)
P0.04: U1.6 (P0.04/AIN2)
P0.05: U1.7 (P0.05/AIN3)
P0.06: U1.8 (P0.06)
P0.07: U1.9 (P0.07)
P0.08: U1.10 (P0.08)
P0.09: U1.11 (P0.09)
P0.10: U1.12 (P0.10)
P0.11: U1.14 (P0.11)
P0.12: U1.15 (P0.12)
P0.13: U1.16 (P0.13)
P0.14: U1.17 (P0.14)
P0.15: U1.18 (P0.15)
P0.16: U1.19 (P0.16)
P0.17: U1.20 (P0.17)
P0.18/SWO: U1.21 (P0.19)
P0.19: U1.22 (P0.19)
P0.20: U1.23 (P0.20)
P0.21/RESET: U1.24 (P0.21/RESET)
P0.22: U1.27 (P0.22)
P0.23: U1.28 (P0.23)
P0.24: U1.29 (P0.24)
P0.25: U1.37 (P0.25)
P0.26: U1.38 (P0.26)
P0.27: U1.39 (P0.27)
P0.28: U1.40 (P0.28/AIN4)
P0.29: U1.41 (P0.29/AIN5)
P0.30: U1.42 (P0.30/AIN6)
P0.31: U1.43 (P031/AIN7)
RF: L1.2
SWDCLK: U1.25 (SWDCLK)
SWDIO: U1.26 (SWDIO)
VDD_P3V3: C5.1, C8.1, C9.1, U1.13 (VDD), U1.36 (VDD), U1.48 (VDD)
X1: C1.1, U1.34 (XC1), X1.1

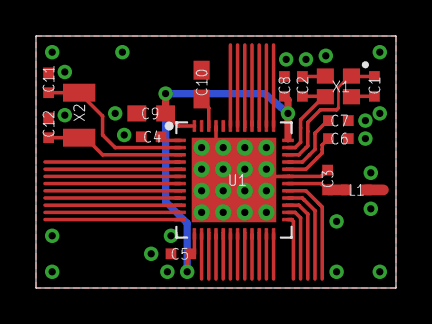
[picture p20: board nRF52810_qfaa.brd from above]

Board: 2 copper layers, 20.0 x 14.0 mm, 16 parts (0 on the bottom side), 11 nets.

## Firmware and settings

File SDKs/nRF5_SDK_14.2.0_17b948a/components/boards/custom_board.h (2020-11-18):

/**
 * Copyright (c) 2017 - 2018, Nordic Semiconductor ASA
 * 
 * All rights reserved.
 * 
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
 * 3. Neither the name of Nordic Semiconductor ASA nor the names of its
 *    contributors may be used to endorse or promote products derived from this
 *    software without specific prior written permission.
 * 
 * 4. This software, with or without modification, must only be used with a
 *    Nordic Semiconductor ASA integrated circuit.
 * 
 * 5. Any software provided in binary form under this license must not be reverse
 *    engineered, decompiled, modified and/or disassembled.
 * 
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
 */
#ifndef PCA10059_H
#define PCA10059_H

#ifdef __cplusplus
extern "C" {
#endif

#include "nrf_gpio.h"

// LED definitions for Armature Joint PCB V1.1
// Each LED color is considered a separate LED
#define LEDS_NUMBER    3

#define LED1_R         NRF_GPIO_PIN_MAP(0,25) //R4
#define LED1_G         NRF_GPIO_PIN_MAP(0,28) //R5
#define LED1_B         NRF_GPIO_PIN_MAP(0,30) //R3

#define LED_1          LED1_G
#define LED_2          LED1_R
#define LED_3          LED1_G


#define LEDS_ACTIVE_STATE 0

#define LEDS_LIST { LED_1, LED_2, LED_3 }

#define LEDS_INV_MASK  LEDS_MASK

#define BSP_LED_1      LED_1
#define BSP_LED_2      LED_2
#define BSP_LED_3      LED_3

// There is only one button for the application
// as the second button is used for a RESET.
#define BUTTONS_NUMBER 0

//#define BUTTON_1       NRF_GPIO_PIN_MAP(1,6)
//#define BUTTON_PULL    NRF_GPIO_PIN_PULLUP

//#define BUTTONS_ACTIVE_STATE 0

//#define BUTTONS_LIST { BUTTON_1 }

//#define BSP_BUTTON_0   BUTTON_1

#define BSP_SELF_PINRESET_PIN NRF_GPIO_PIN_MAP(0,21)

#define HWFC           true

// Arduino board mappings
//#define ARDUINO_SCL_PIN             NRF_GPIO_PIN_MAP(0, 15)    // SCL signal pin
//#define ARDUINO_SDA_PIN             NRF_GPIO_PIN_MAP(0, 16)    // SDA signal pin



#ifdef __cplusplus
}
#endif

#endif // PCA10059_H

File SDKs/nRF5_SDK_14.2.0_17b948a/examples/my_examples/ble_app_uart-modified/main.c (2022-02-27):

/**
 * Copyright (c) 2014 - 2017, Nordic Semiconductor ASA
 * 
 * All rights reserved.
 * 
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
 * 3. Neither the name of Nordic Semiconductor ASA nor the names of its
 *    contributors may be used to endorse or promote products derived from this
 *    software without specific prior written permission.
 * 
 * 4. This software, with or without modification, must only be used with a
 *    Nordic Semiconductor ASA integrated circuit.
 * 
 * 5. Any software provided in binary form under this license must not be reverse
 *    engineered, decompiled, modified and/or disassembled.
 * 
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
 */
/** @file
 *
 * @defgroup ble_sdk_uart_over_ble_main main.c
 * @{
 * @ingroup  ble_sdk_app_nus_eval
 * @brief    UART over BLE application main file.
 *
 * This file contains the source code for a sample application that uses the Nordic UART service.
 * This application uses the @ref srvlib_conn_params module.
 */



#include <stdint.h>
#include <string.h>
#include <stdio.h> 
#include "nordic_common.h"
#include "nrf.h"
#include "ble_hci.h"
#include "ble_advdata.h"
#include "ble_advertising.h"
#include "ble_conn_params.h"
#include "nrf_sdh.h"
#include "nrf_sdh_soc.h"
#include "nrf_sdh_ble.h"
#include "nrf_ble_gatt.h"
#include "app_timer.h"
#include "ble_nus.h"
#include "app_uart.h"
#include "app_util_platform.h"
#include "bsp_btn_ble.h"

#if defined (UART_PRESENT)
#include "nrf_uart.h"
#endif
#if defined (UARTE_PRESENT)
#include "nrf_uarte.h"
#endif

#include "nrf_log.h"
#include "nrf_log_ctrl.h"
#include "nrf_log_default_backends.h"

//***Area for variables foreign to the original program***
APP_TIMER_DEF(test_timer_id);
#define test_delay                      200

uint8_t data_array[5] = {'h','e','l','l','o'};

#define APP_BLE_CONN_CFG_TAG            1                                           /**< A tag identifying the SoftDevice BLE configuration. */

#define APP_FEATURE_NOT_SUPPORTED       BLE_GATT_STATUS_ATTERR_APP_BEGIN + 2        /**< Reply when unsupported features are requested. */

#define DEVICE_NAME                     "Nordic_UART"                               /**< Name of device. Will be included in the advertising data. */
#define NUS_SERVICE_UUID_TYPE           BLE_UUID_TYPE_VENDOR_BEGIN                  /**< UUID type for the Nordic UART Service (vendor specific). */

#define APP_BLE_OBSERVER_PRIO           3                                           /**< Application's BLE observer priority. You shouldn't need to modify this value. */

#define APP_ADV_INTERVAL                64                                          /**< The advertising interval (in units of 0.625 ms. This value corresponds to 40 ms). */
#define APP_ADV_TIMEOUT_IN_SECONDS      180                                         /**< The advertising timeout (in units of seconds). */

#define MIN_CONN_INTERVAL               MSEC_TO_UNITS(20, UNIT_1_25_MS)             /**< Minimum acceptable connection interval (20 ms), Connection interval uses 1.25 ms units. */
#define MAX_CONN_INTERVAL               MSEC_TO_UNITS(75, UNIT_1_25_MS)             /**< Maximum acceptable connection interval (75 ms), Connection interval uses 1.25 ms units. */
#define SLAVE_LATENCY                   0                                           /**< Slave latency. */
#define CONN_SUP_TIMEOUT                MSEC_TO_UNITS(4000, UNIT_10_MS)             /**< Connection supervisory timeout (4 seconds), Supervision Timeout uses 10 ms units. */
#define FIRST_CONN_PARAMS_UPDATE_DELAY  APP_TIMER_TICKS(5000)                       /**< Time from initiating event (connect or start of notification) to first time sd_ble_gap_conn_param_update is called (5 seconds). */
#define NEXT_CONN_PARAMS_UPDATE_DELAY   APP_TIMER_TICKS(30000)                      /**< Time between each call to sd_ble_gap_conn_param_update after the first call (30 seconds). */
#define MAX_CONN_PARAMS_UPDATE_COUNT    3                                           /**< Number of attempts before giving up the connection parameter negotiation. */

#define DEAD_BEEF                       0xDEADBEEF                                  /**< Value used as error code on stack dump, can be used to identify stack location on stack unwind. */

#define UART_TX_BUF_SIZE                256                                         /**< UART TX buffer size. */
#define UART_RX_BUF_SIZE                256                                         /**< UART RX buffer size. */


BLE_NUS_DEF(m_nus);                                                                 /**< BLE NUS service instance. */
NRF_BLE_GATT_DEF(m_gatt);                                                           /**< GATT module instance. */
BLE_ADVERTISING_DEF(m_advertising);                                                 /**< Advertising module instance. */

static uint16_t   m_conn_handle          = BLE_CONN_HANDLE_INVALID;                 /**< Handle of the current connection. */
static uint16_t   m_ble_nus_max_data_len = BLE_GATT_ATT_MTU_DEFAULT - 3;            /**< Maximum length of data (in bytes) that can be transmitted to the peer by the Nordic UART service module. */
static ble_uuid_t m_adv_uuids[]          =                                          /**< Universally unique service identifier. */
{
    {BLE_UUID_NUS_SERVICE, NUS_SERVICE_UUID_TYPE}
};


/**@brief Function for assert macro callback.
 *
 * @details This function will be called in case of an assert in the SoftDevice.
 *
 * @warning This handler is an example only and does not fit a final product. You need to analyse
 *          how your product is supposed to react in case of Assert.
 * @warning On assert from the SoftDevice, the system can only recover on reset.
 *
 * @param[in] line_num    Line number of the failing ASSERT call.
 * @param[in] p_file_name File name of the failing ASSERT call.
 */
void assert_nrf_callback(uint16_t line_num, const uint8_t * p_file_name)
{
    app_error_handler(DEAD_BEEF, line_num, p_file_name);
}


/**@brief Function for the GAP initialization.
 *
 * @details This function will set up all the necessary GAP (Generic Access Profile) parameters of
 *          the device. It also sets the permissions and appearance.
 */
static void gap_params_init(void)
{
    uint32_t                err_code;
    ble_gap_conn_params_t   gap_conn_params;
    ble_gap_conn_sec_mode_t sec_mode;

    BLE_GAP_CONN_SEC_MODE_SET_OPEN(&sec_mode);

    err_code = sd_ble_gap_device_name_set(&sec_mode,
                                          (const uint8_t *) DEVICE_NAME,
                                          strlen(DEVICE_NAME));
    APP_ERROR_CHECK(err_code);

    memset(&gap_conn_params, 0, sizeof(gap_conn_params));

    gap_conn_params.min_conn_interval = MIN_CONN_INTERVAL;
    gap_conn_params.max_conn_interval = MAX_CONN_INTERVAL;
    gap_conn_params.slave_latency     = SLAVE_LATENCY;
    gap_conn_params.conn_sup_timeout  = CONN_SUP_TIMEOUT;

    err_code = sd_ble_gap_ppcp_set(&gap_conn_params);
    APP_ERROR_CHECK(err_code);
}


/**@brief Function for handling the data from the Nordic UART Service.
 *
 * @details This function will process the data received from the Nordic UART BLE Service and send
 *          it to the UART module.
 *
 * @param[in] p_nus    Nordic UART Service structure.
 * @param[in] p_data   Data to be send to UART module.
 * @param[in] length   Length of the data.
 */
/**@snippet [Handling the data received over BLE] */
static void nus_data_handler(ble_nus_evt_t * p_evt)
{

    if (p_evt->type == BLE_NUS_EVT_RX_DATA)
    {
        uint32_t err_code;

        NRF_LOG_DEBUG("Received data from BLE NUS. Writing data on UART.");
        NRF_LOG_HEXDUMP_DEBUG(p_evt->params.rx_data.p_data, p_evt->params.rx_data.length);

        for (uint32_t i = 0; i < p_evt->params.rx_data.length; i++)
        {
            do
            {
                err_code = app_uart_put(p_evt->params.rx_data.p_data[i]);
                if ((err_code != NRF_SUCCESS) && (err_code != NRF_ERROR_BUSY))
                {
                    NRF_LOG_ERROR("Failed receiving NUS message. Error 0x%x. ", err_code);
                    APP_ERROR_CHECK(err_code);
                }
            } while (err_code == NRF_ERROR_BUSY);
        }
        if (p_evt->params.rx_data.p_data[p_evt->params.rx_data.length-1] == '\r')
        {
            while (app_uart_put('\n') == NRF_ERROR_BUSY);
        }
    }

}
/**@snippet [Handling the data received over BLE] */


/**@brief Function for initializing services that will be used by the application.
 */
static void services_init(void)
{
    uint32_t       err_code;
    ble_nus_init_t nus_init;

    memset(&nus_init, 0, sizeof(nus_init));

    nus_init.data_handler = nus_data_handler;

    err_code = ble_nus_init(&m_nus, &nus_init);
    APP_ERROR_CHECK(err_code);
}


/**@brief Function for handling an event from the Connection Parameters Module.
 *
 * @details This function will be called for all events in the Connection Parameters Module
 *          which are passed to the application.
 *
 * @note All this function does is to disconnect. This could have been done by simply setting
 *       the disconnect_on_fail config parameter, but instead we use the event handler
 *       mechanism to demonstrate its use.
 *
 * @param[in] p_evt  Event received from the Connection Parameters Module.
 */
static void on_conn_params_evt(ble_conn_params_evt_t * p_evt)
{
    uint32_t err_code;

    if (p_evt->evt_type == BLE_CONN_PARAMS_EVT_FAILED)
    {
        err_code = sd_ble_gap_disconnect(m_conn_handle, BLE_HCI_CONN_INTERVAL_UNACCEPTABLE);
        APP_ERROR_CHECK(err_code);
    }
}


/**@brief Function for handling errors from the Connection Parameters module.
 *
 * @param[in] nrf_error  Error code containing information about what went wrong.
 */
static void conn_params_error_handler(uint32_t nrf_error)
{
    APP_ERROR_HANDLER(nrf_error);
}


/**@brief Function for initializing the Connection Parameters module.
 */
static void conn_params_init(void)
{
    uint32_t               err_code;
    ble_conn_params_init_t cp_init;

    memset(&cp_init, 0, sizeof(cp_init));

    cp_init.p_conn_params                  = NULL;
    cp_init.first_conn_params_update_delay = FIRST_CONN_PARAMS_UPDATE_DELAY;
    cp_init.next_conn_params_update_delay  = NEXT_CONN_PARAMS_UPDATE_DELAY;
    cp_init.max_conn_params_update_count   = MAX_CONN_PARAMS_UPDATE_COUNT;
    cp_init.start_on_notify_cccd_handle    = BLE_GATT_HANDLE_INVALID;
    cp_init.disconnect_on_fail             = false;
    cp_init.evt_handler                    = on_conn_params_evt;
    cp_init.error_handler                  = conn_params_error_handler;

    err_code = ble_conn_params_init(&cp_init);
    APP_ERROR_CHECK(err_code);
}


/**@brief Function for putting the chip into sleep mode.
 *
 * @note This function will not return.
 */
static void sleep_mode_enter(void)
{
    uint32_t err_code = bsp_indication_set(BSP_INDICATE_IDLE);
    APP_ERROR_CHECK(err_code);

    // Prepare wakeup buttons.
    err_code = bsp_btn_ble_sleep_mode_prepare();
    APP_ERROR_CHECK(err_code);

    // Go to system-off mode (this function will not return; wakeup will cause a reset).
    err_code = sd_power_system_off();
    APP_ERROR_CHECK(err_code);
}


/**@brief Function for handling advertising events.
 *
 * @details This function will be called for advertising events which are passed to the application.
 *
 * @param[in] ble_adv_evt  Advertising event.
 */
static void on_adv_evt(ble_adv_evt_t ble_adv_evt)
{
    uint32_t err_code;

    switch (ble_adv_evt)
    {
        case BLE_ADV_EVT_FAST:
            err_code = bsp_indication_set(BSP_INDICATE_ADVERTISING);
            APP_ERROR_CHECK(err_code);
            break;
        case BLE_ADV_EVT_IDLE:
            sleep_mode_enter();
            break;
        default:
            break;
    }
}


/**@brief Function for handling BLE events.
 *
 * @param[in]   p_ble_evt   Bluetooth stack event.
 * @param[in]   p_context   Unused.
 */
static void ble_evt_handler(ble_evt_t const * p_ble_evt, void * p_context)
{
    uint32_t err_code;

    switch (p_ble_evt->header.evt_id)
    {
        case BLE_GAP_EVT_CONNECTED:
            NRF_LOG_INFO("Connected");
            err_code = bsp_indication_set(BSP_INDICATE_CONNECTED);
            APP_ERROR_CHECK(err_code);
            m_conn_handle = p_ble_evt->evt.gap_evt.conn_handle;
            break;

        case BLE_GAP_EVT_DISCONNECTED:
            NRF_LOG_INFO("Disconnected");
            // LED indication will be changed when advertising starts.
            m_conn_handle = BLE_CONN_HANDLE_INVALID;
            break;

#ifndef S140
        case BLE_GAP_EVT_PHY_UPDATE_REQUEST:
        {
            NRF_LOG_DEBUG("PHY update request.");
            ble_gap_phys_t const phys =
            {
                .rx_phys = BLE_GAP_PHY_AUTO,
                .tx_phys = BLE_GAP_PHY_AUTO,
            };
            err_code = sd_ble_gap_phy_update(p_ble_evt->evt.gap_evt.conn_handle, &phys);
            APP_ERROR_CHECK(err_code);
        } break;
#endif

        case BLE_GAP_EVT_SEC_PARAMS_REQUEST:
            // Pairing not supported
            err_code = sd_ble_gap_sec_params_reply(m_conn_handle, BLE_GAP_SEC_STATUS_PAIRING_NOT_SUPP, NULL, NULL);
            APP_ERROR_CHECK(err_code);
            break;
#if !defined (S112)
         case BLE_GAP_EVT_DATA_LENGTH_UPDATE_REQUEST:
        {
            ble_gap_data_length_params_t dl_params;

            // Clearing the struct will effectivly set members to @ref BLE_GAP_DATA_LENGTH_AUTO
            memset(&dl_params, 0, sizeof(ble_gap_data_length_params_t));
            err_code = sd_ble_gap_data_length_update(p_ble_evt->evt.gap_evt.conn_handle, &dl_params, NULL);
            APP_ERROR_CHECK(err_code);
        } break;
#endif //!defined (S112)
        case BLE_GATTS_EVT_SYS_ATTR_MISSING:
            // No system attributes have been stored.
            err_code = sd_ble_gatts_sys_attr_set(m_conn_handle, NULL, 0, 0);
            APP_ERROR_CHECK(err_code);
            break;

        case BLE_GATTC_EVT_TIMEOUT:
            // Disconnect on GATT Client timeout event.
            err_code = sd_ble_gap_disconnect(p_ble_evt->evt.gattc_evt.conn_handle,
                                             BLE_HCI_REMOTE_USER_TERMINATED_CONNECTION);
            APP_ERROR_CHECK(err_code);
            break;

        case BLE_GATTS_EVT_TIMEOUT:
            // Disconnect on GATT Server timeout event.
            err_code = sd_ble_gap_disconnect(p_ble_evt->evt.gatts_evt.conn_handle,
                                             BLE_HCI_REMOTE_USER_TERMINATED_CONNECTION);
            APP_ERROR_CHECK(err_code);
            break;

        case BLE_EVT_USER_MEM_REQUEST:
            err_code = sd_ble_user_mem_reply(p_ble_evt->evt.gattc_evt.conn_handle, NULL);
            APP_ERROR_CHECK(err_code);
            break;

        case BLE_GATTS_EVT_RW_AUTHORIZE_REQUEST:
        {
            ble_gatts_evt_rw_authorize_request_t  req;
            ble_gatts_rw_authorize_reply_params_t auth_reply;

            req = p_ble_evt->evt.gatts_evt.params.authorize_request;

            if (req.type != BLE_GATTS_AUTHORIZE_TYPE_INVALID)
            {
                if ((req.request.write.op == BLE_GATTS_OP_PREP_WRITE_REQ)     ||
                    (req.request.write.op == BLE_GATTS_OP_EXEC_WRITE_REQ_NOW) ||
                    (req.request.write.op == BLE_GATTS_OP_EXEC_WRITE_REQ_CANCEL))
                {
                    if (req.type == BLE_GATTS_AUTHORIZE_TYPE_WRITE)
                    {
                        auth_reply.type = BLE_GATTS_AUTHORIZE_TYPE_WRITE;
                    }
                    else
                    {
                        auth_reply.type = BLE_GATTS_AUTHORIZE_TYPE_READ;
                    }
                    auth_reply.params.write.gatt_status = APP_FEATURE_NOT_SUPPORTED;
                    err_code = sd_ble_gatts_rw_authorize_reply(p_ble_evt->evt.gatts_evt.conn_handle,
                                                               &auth_reply);
                    APP_ERROR_CHECK(err_code);
                }
            }
        } break; // BLE_GATTS_EVT_RW_AUTHORIZE_REQUEST

        default:
            // No implementation needed.
            break;
    }
}


/**@brief Function for the SoftDevice initialization.
 *
 * @details This function initializes the SoftDevice and the BLE event interrupt.
 */
static void ble_stack_init(void)
{
    ret_code_t err_code;

    err_code = nrf_sdh_enable_request();
    APP_ERROR_CHECK(err_code);

    // Configure the BLE stack using the default settings.
    // Fetch the start address of the application RAM.
    uint32_t ram_start = 0;
    err_code = nrf_sdh_ble_default_cfg_set(APP_BLE_CONN_CFG_TAG, &ram_start);
    APP_ERROR_CHECK(err_code);

    // Enable BLE stack.
    err_code = nrf_sdh_ble_enable(&ram_start);
    APP_ERROR_CHECK(err_code);

    // Register a handler for BLE events.
    NRF_SDH_BLE_OBSERVER(m_ble_observer, APP_BLE_OBSERVER_PRIO, ble_evt_handler, NULL);
}


/**@brief Function for handling events from the GATT library. */
void gatt_evt_handler(nrf_ble_gatt_t * p_gatt, nrf_ble_gatt_evt_t const * p_evt)
{
    if ((m_conn_handle == p_evt->conn_handle) && (p_evt->evt_id == NRF_BLE_GATT_EVT_ATT_MTU_UPDATED))
    {
        m_ble_nus_max_data_len = p_evt->params.att_mtu_effective - OPCODE_LENGTH - HANDLE_LENGTH;
        NRF_LOG_INFO("Data len is set to 0x%X(%d)", m_ble_nus_max_data_len, m_ble_nus_max_data_len);
    }
    NRF_LOG_DEBUG("ATT MTU exchange completed. central 0x%x peripheral 0x%x",
                  p_gatt->att_mtu_desired_central,
                  p_gatt->att_mtu_desired_periph);
}


/**@brief Function for initializing the GATT library. */
void gatt_init(void)
{
    ret_code_t err_code;

    err_code = nrf_ble_gatt_init(&m_gatt, gatt_evt_handler);
    APP_ERROR_CHECK(err_code);

    err_code = nrf_ble_gatt_att_mtu_periph_set(&m_gatt, 64);
    APP_ERROR_CHECK(err_code);
}


/**@brief Function for handling events from the BSP module.
 *
 * @param[in]   event   Event generated by button press.
 */
void bsp_event_handler(bsp_event_t event)
{
    uint32_t err_code;
    switch (event)
    {
        case BSP_EVENT_SLEEP:
            sleep_mode_enter();
            break;

        case BSP_EVENT_DISCONNECT:
            err_code = sd_ble_gap_disconnect(m_conn_handle, BLE_HCI_REMOTE_USER_TERMINATED_CONNECTION);
            if (err_code != NRF_ERROR_INVALID_STATE)
            {
                APP_ERROR_CHECK(err_code);
            }
            break;

        case BSP_EVENT_WHITELIST_OFF:
            if (m_conn_handle == BLE_CONN_HANDLE_INVALID)
            {
                err_code = ble_advertising_restart_without_whitelist(&m_advertising);
                if (err_code != NRF_ERROR_INVALID_STATE)
                {
                    APP_ERROR_CHECK(err_code);
                }
            }
            break;

        default:
            break;
    }
}


/**@brief   Function for handling app_uart events.
 *
 * @details This function will receive a single character from the app_uart module and append it to
 *          a string. The string will be be sent over BLE when the last character received was a
 *          'new line' '\n' (hex 0x0A) or if the string has reached the maximum data length.
 */
/**@snippet [Handling the data received over UART] */
void uart_event_handle(app_uart_evt_t * p_event)
{
    static uint8_t data_array[BLE_NUS_MAX_DATA_LEN];
    static uint8_t index = 0;
    uint32_t       err_code;

    switch (p_event->evt_type)
    {
        case APP_UART_DATA_READY:
            UNUSED_VARIABLE(app_uart_get(&data_array[index]));
            index++;

            if ((data_array[index - 1] == '\n') || (index >= (m_ble_nus_max_data_len)))
            {
                NRF_LOG_DEBUG("Ready to send data over BLE NUS");
                NRF_LOG_HEXDUMP_DEBUG(data_array, index);

                do
                {
                    uint16_t length = (uint16_t)index;
                    err_code = ble_nus_string_send(&m_nus, data_array, &length);
                    if ( (err_code != NRF_ERROR_INVALID_STATE) && (err_code != NRF_ERROR_BUSY) )
                    {
                        APP_ERROR_CHECK(err_code);
                    }
                } while (err_code == NRF_ERROR_BUSY);

                index = 0;
            }
            break;

        case APP_UART_COMMUNICATION_ERROR:
            APP_ERROR_HANDLER(p_event->data.error_communication);
            break;

        case APP_UART_FIFO_ERROR:
            APP_ERROR_HANDLER(p_event->data.error_code);
            break;

        default:
            break;
    }
}
/**@snippet [Handling the data received over UART] */
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
int main(void)
{
    uint32_t err_code;
    bool     erase_bonds;

    // Initialize.
    err_code = app_timer_init();
    APP_ERROR_CHECK(err_code);

    //uart_init();
    log_init();

    buttons_leds_init(&erase_bonds);
    ble_stack_init();
    gap_params_init();
    gatt_init();
    services_init();
    advertising_init();
    conn_params_init();

    printf("\r\nUART printf Start!\r\n");
    NRF_LOG_INFO("UART log Start!");
    err_code = ble_advertising_start(&m_advertising, BLE_ADV_MODE_FAST);
    APP_ERROR_CHECK(err_code);

    //err_code =
	   //app_timer_create(&test_timer_id, APP_TIMER_MODE_SINGLE_SHOT, test_timer_handler);
    
    //testing the repeated timer mode (the timer should restart each time it expires)
    err_code = app_timer_create(&test_timer_id, APP_TIMER_MODE_REPEATED, test_timer_handler);
    
    //Start the timer
    err_code = app_timer_start(test_timer_id, APP_TIMER_TICKS(test_delay), NULL);


    // Enter main loop.
    for (;;)
    {  
        UNUSED_RETURN_VALUE(NRF_LOG_PROCESS());
        power_manage();
    }
}


/**
 * @}
 */

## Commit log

2020-11-18 added v14.2 SDK
    [config.txt]
2022-02-27 added PDF of eagle schematic

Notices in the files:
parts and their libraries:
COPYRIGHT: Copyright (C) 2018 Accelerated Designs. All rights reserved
